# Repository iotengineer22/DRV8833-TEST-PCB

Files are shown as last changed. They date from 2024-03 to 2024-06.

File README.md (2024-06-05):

# PCB-DRV8833-TEST
DRV8833-PCB-KiCad-DATA
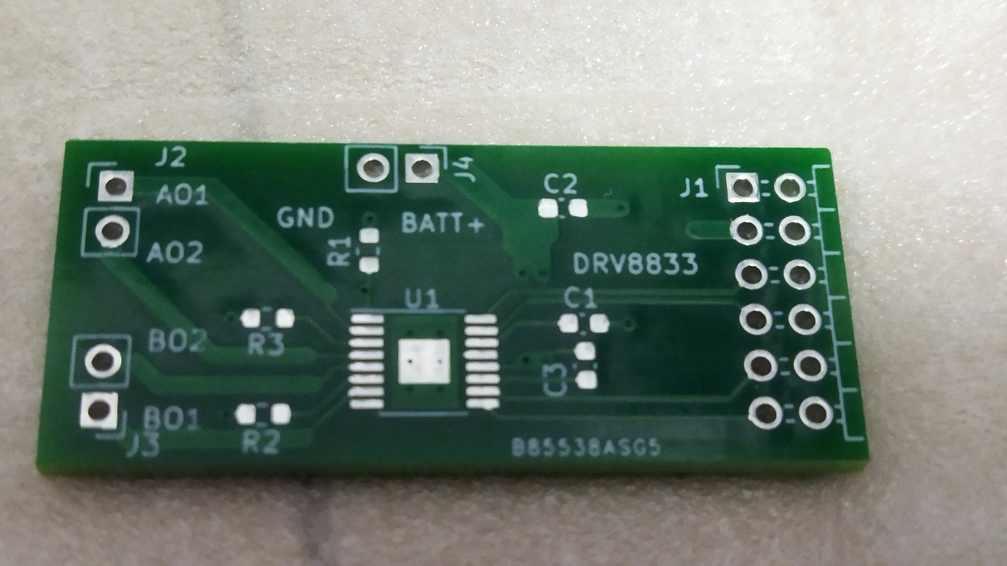
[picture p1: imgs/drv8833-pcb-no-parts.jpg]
no-parts

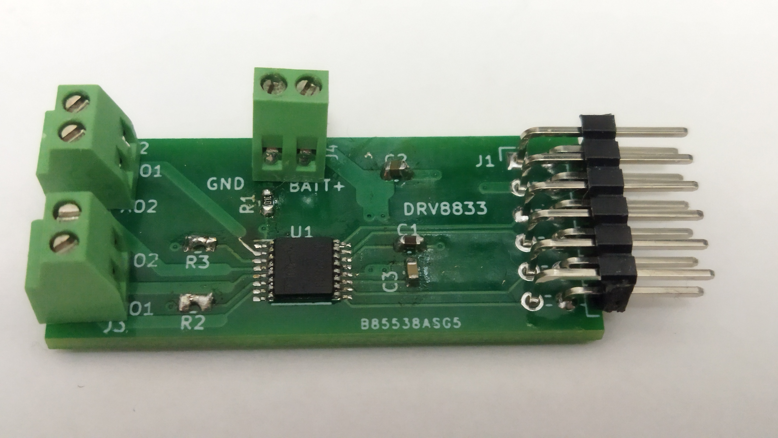
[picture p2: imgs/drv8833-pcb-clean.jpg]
overview


# Schematics
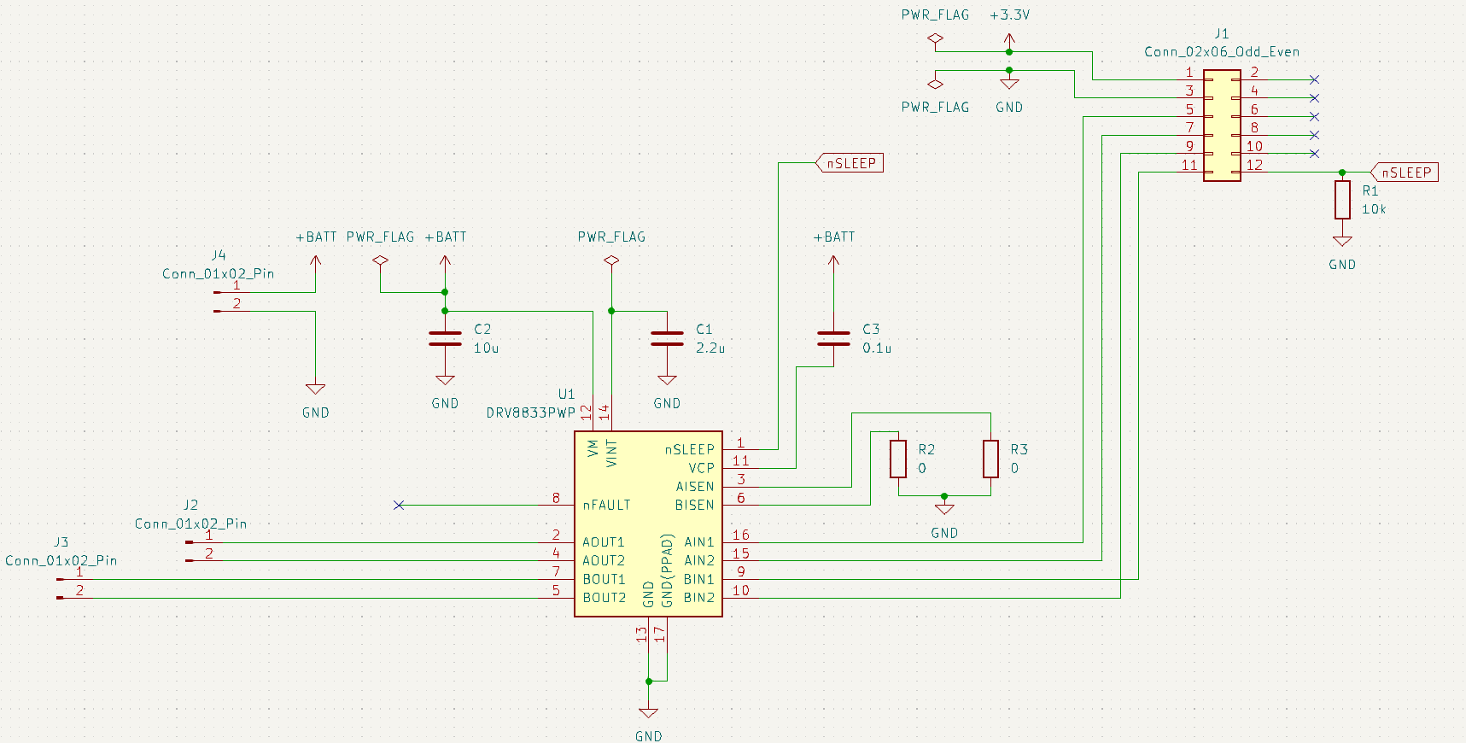
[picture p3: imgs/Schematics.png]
schematics


# Artwork
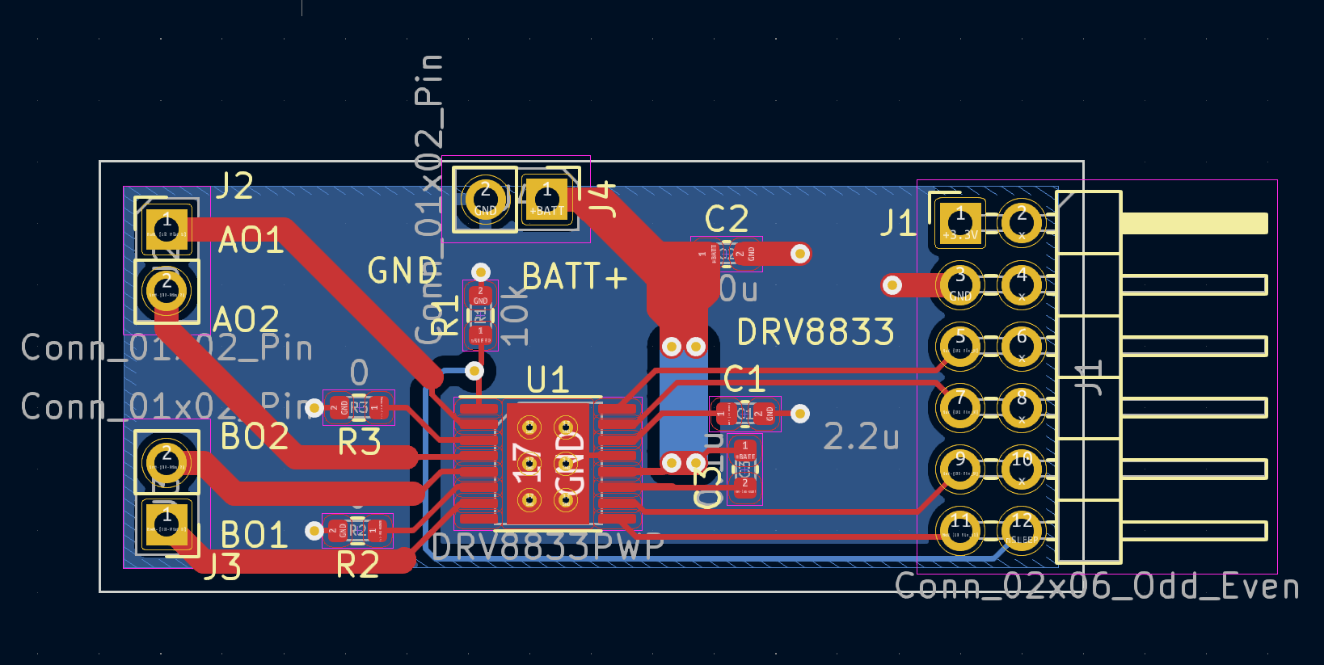
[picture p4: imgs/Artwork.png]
aw1


# BOM-List
Motor-Driver-PCB --- Original-PCB

Motor-Driver-IC(U1) --- DRV8833PWPR

Resistor_SMD(R1) --- 0603_1608Metric_10k

Resistor_SMD(R2.R3) --- 0603_1608Metric_0 (or short-bar)

Capacitor_SMD(C1) --- 0603_1608Metric_2.2u

Capacitor_SMD(C2) --- 0603_1608Metric_10u

Capacitor_SMD(C3) --- 0603_1608Metric_0.1u

PinHeader_2x06(J1) -- 2x06_P2.54mm_Horizontal

PinHeader_1x02(J2,J3,J4) --- 1x02_P2.54mm_Vertical

# PCB specifications
Zip the "drv8833-pcb" folder and send it to any PCB fabrication company (e.g., PCBGOGO).

The PCB specifications match the default settings of most fabrication companies. Just enter the dimensions and proceed with the order.

PCB Size: 17.78mm x 40.64mm

Layers: 2

Material: FR-4

FR4-TG: TG150-160

Thickness: 1.6mm

Min track/spacing: 6/6mil

Minimum hole size: 0.3mm

Solder mask: Green

Silkscreen: White

# DEMO
dc_test

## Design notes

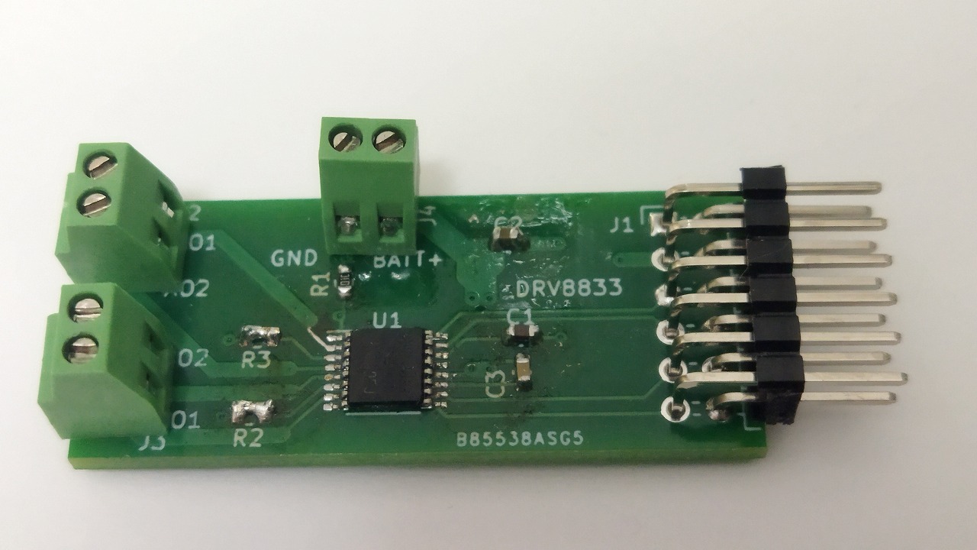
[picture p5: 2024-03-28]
imgs/drv8833-pcb.jpg

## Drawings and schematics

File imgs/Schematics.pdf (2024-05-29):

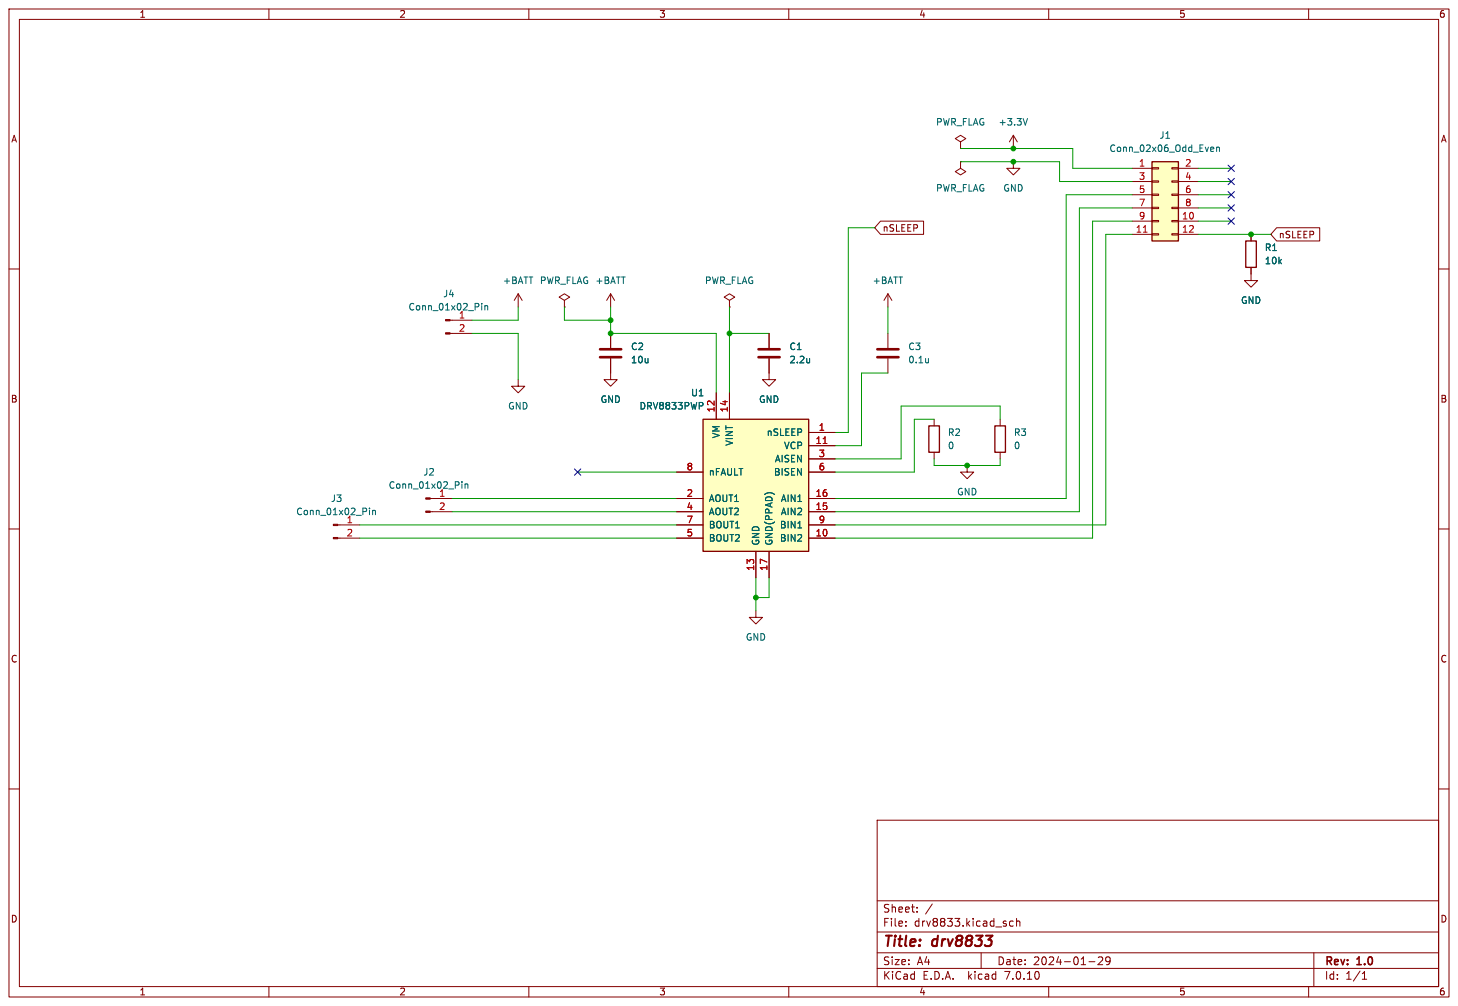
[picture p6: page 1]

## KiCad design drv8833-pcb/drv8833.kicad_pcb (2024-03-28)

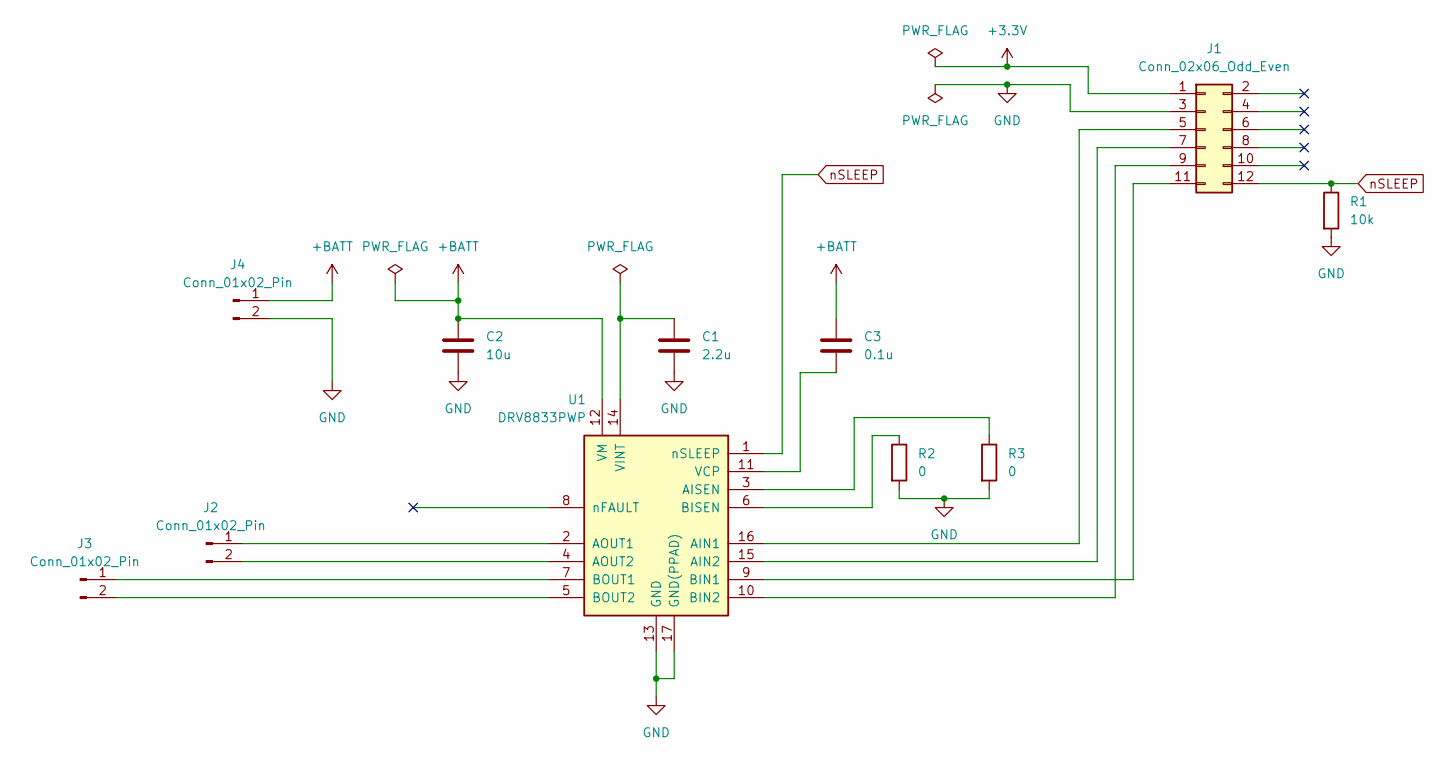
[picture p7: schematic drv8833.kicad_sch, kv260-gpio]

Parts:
C1: 2.2u; C_0603_1608Metric
C2: 10u; C_0603_1608Metric
C3: 0.1u; C_0603_1608Metric
J1: Conn_02x06_Odd_Even; PinHeader_2x06_P2.54mm_Horizontal
J2, J3, J4: Conn_01x02_Pin; PinHeader_1x02_P2.54mm_Vertical
R1: 10k; R_0603_1608Metric
R2, R3: 0; R_0603_1608Metric
U1: DRV8833PWP; HTSSOP-16-1EP_4.4x5mm_P0.65mm_EP3.4x5mm_Mask2.46x2.31mm_The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

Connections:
+3.3V: J1.1
+BATT: C2.1, C3.1, J4.1, U1.12 (VM)
GND: C1.2, C2.2, J1.3, J4.2, R1.2, R2.2, R3.2, U1.13 (GND), U1.17 (GND(PPAD))
unnamed: J1.5, U1.16 (AIN1)
unnamed: J1.7, U1.15 (AIN2)
unnamed: J1.9, U1.10 (BIN2)
unnamed: J1.11, U1.9 (BIN1)
unnamed: J2.1, U1.2 (AOUT1)
unnamed: J2.2, U1.4 (AOUT2)
unnamed: J3.1, U1.7 (BOUT1)
unnamed: J3.2, U1.5 (BOUT2)
unnamed: R3.1, U1.3 (AISEN)
unnamed: R2.1, U1.6 (BISEN)
unnamed: C3.2, U1.11 (VCP)
unnamed: C1.1, U1.14 (VINT)
nSLEEP: J1.12, R1.1, U1.1 (nSLEEP)

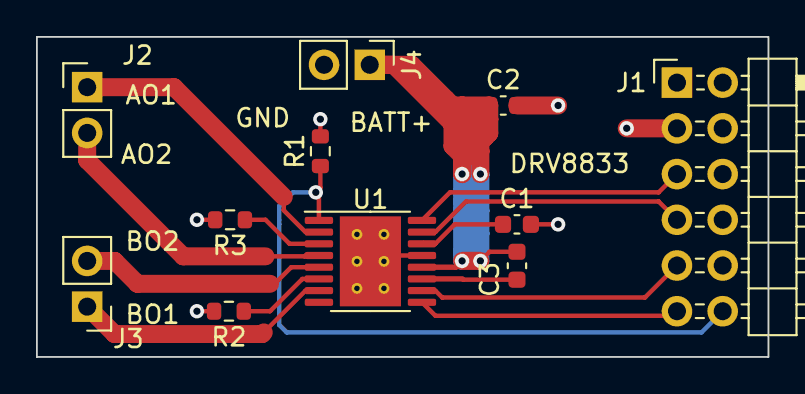
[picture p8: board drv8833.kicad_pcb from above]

Board: 2 copper layers, 40.6 x 17.8 mm, 11 parts (0 on the bottom side), 15 nets.
